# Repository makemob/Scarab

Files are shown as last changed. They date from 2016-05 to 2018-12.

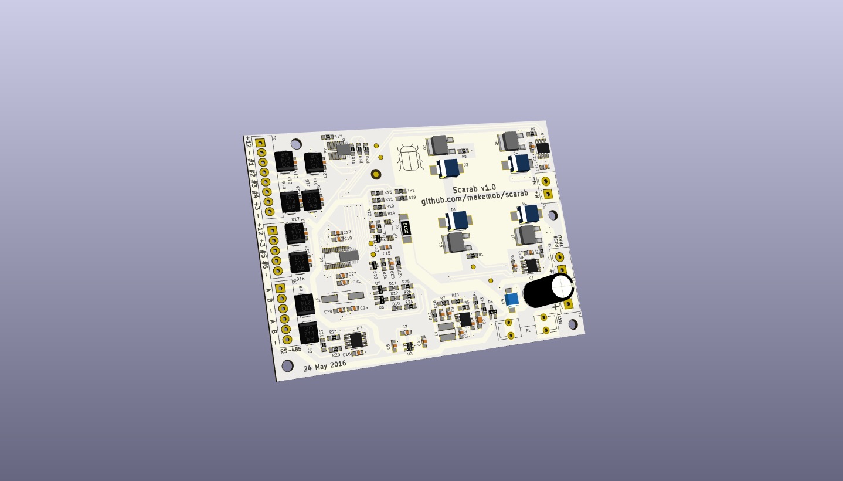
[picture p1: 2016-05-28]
v1.0/Docs/Scarab v1.0 3D Front 4.jpg

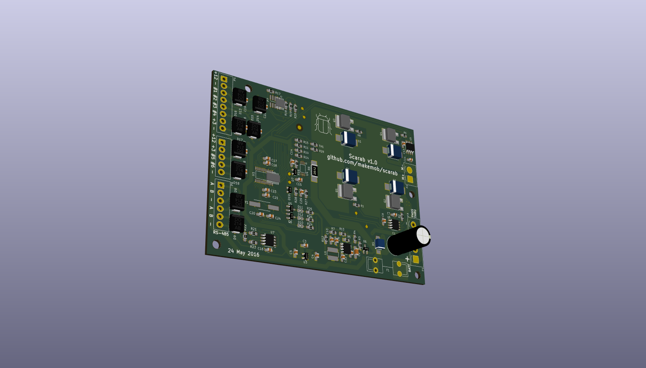
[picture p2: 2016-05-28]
v1.0/Docs/Scarab v1.0 3D Front 1.png

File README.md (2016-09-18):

# Scarab
H-Bridge motor/actuator controller with RS-485 comms

- Based around NXP LPC1114 Microcontroller
- 13-48VDC input (36V nominal)
- 8A average current output
- 12VDC max 200mA auxiliary output
- 3.3VDC auxiliary output ~40mA at 25 deg C, <10mA at 85 deg C
- Good to 85 deg C ambient (in theory)
- RS-485 comms, aux analog and digital I/O
- 3 x indicator LEDs
- NTC temperature sensor
- Battery voltage sensing

All specifications are indicative..

Designed to drive Linak LA-35 linear actuators for the MakeMob UKI - Utility Kinetic Insect project http://makemob.net/portfolio_page/uki-electric-insect-vehicle/

Suitable for all kinds of other clever tricks

Firmware available at http://github.com/makemob/huhu

Licensed under Creative Commons Attribution Share Alike 4.0, https://creativecommons.org/licenses/by-sa/4.0/legalcode.txt

BOM adjustments since v1.0:
- Replace R1, R2, R8, R9 with 100ohm
- Populate D7 (3V zener), C14 (10nF), D15 & D16 (5V TVS), C25 & C26 (100nF)
- RC snubber across motor output may be required to protect gate drivers from overvoltage (it is if you want to run LA-35 actuators at 36V..)

Next time:
- Locating C1 closer to the bridge may improve transients
- BAV99 footprints are wrong, need to jam them on sideways (D6, D7, D19)

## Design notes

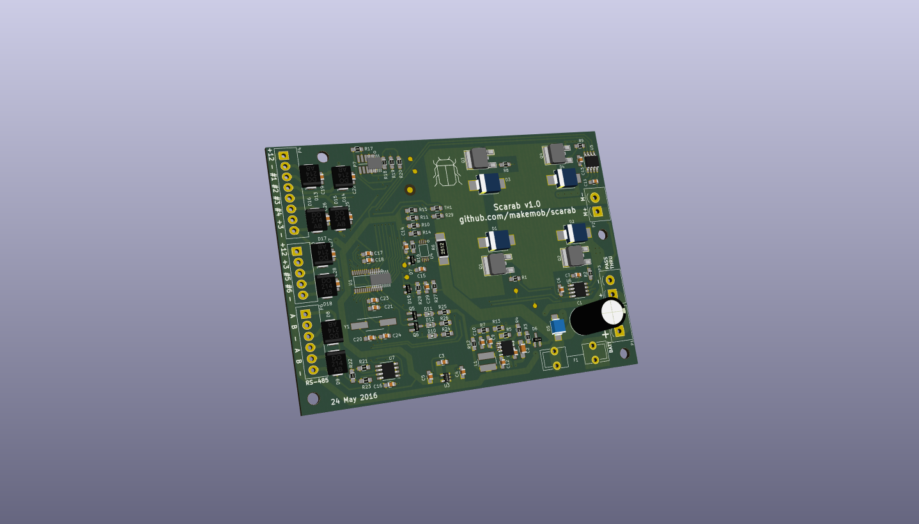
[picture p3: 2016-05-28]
v1.0/Docs/Scarab v1.0 3D Front 3.png

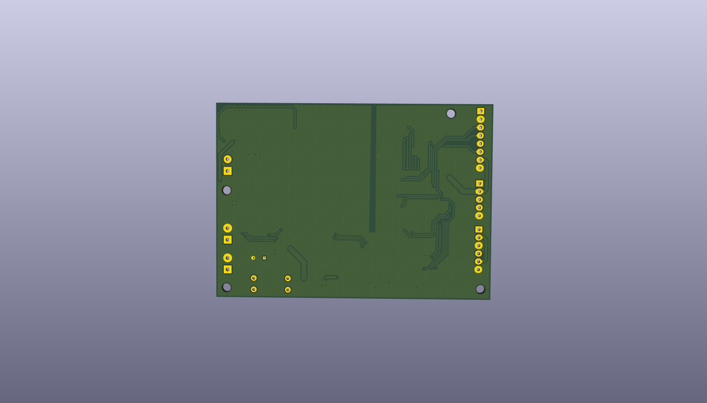
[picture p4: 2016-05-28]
v1.0/Docs/Scarab v1.0 3D Back 1.png

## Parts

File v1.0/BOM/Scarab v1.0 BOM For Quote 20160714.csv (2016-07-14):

Reference | Value | Footprint | Datasheet
P1 | BATT | BugBridgePCBLib:Connector_5.08mm_Pitch_2way
P2 | MOTOR | BugBridgePCBLib:Connector_5.08mm_Pitch_2way
P4 | AUX_A | BugBridgePCBLib:Connector_3.5mm_Pitch_8way
P6 | COMMS | BugBridgePCBLib:Connector_3.5mm_Pitch_6way
P3 | PASSTHRU | BugBridgePCBLib:Connector_5.08mm_Pitch_2way
P5 | AUX_B | BugBridgePCBLib:Connector_3.5mm_Pitch_5way
C8 | 10nF | Capacitors_SMD:C_0805_HandSoldering
C2 | 2.2uF | Capacitors_SMD:C_1206_HandSoldering
C9 | 68pF | Capacitors_SMD:C_0805_HandSoldering
R3 | NF | Resistors_SMD:R_0805_HandSoldering
R4 | NF | Resistors_SMD:R_0805_HandSoldering
R12 | 140k | Resistors_SMD:R_0805_HandSoldering
R13 | 10k | Resistors_SMD:R_0805_HandSoldering
L1 | 220uH 1.57R | BugBridgePCBLib:INDUCTOR_SDR0604
C12 | 10uF | Capacitors_SMD:C_0805_HandSoldering
U2 | TPS54061 | BugBridgePCBLib:VSON8
R7 | 158k | Resistors_SMD:R_0805_HandSoldering
C10 | 750pF | Capacitors_SMD:C_0805_HandSoldering
R5 | 97.6k | Resistors_SMD:R_0805_HandSoldering
F1 | 8A | BugBridgePCBLib:Fuseholder_5x20_Schurter
U3 | MIC5205-3.3YM5 | TO_SOT_Packages_SMD:SOT-23-5
C4 | 1uF | Capacitors_SMD:C_0805_HandSoldering
C3 | NF | Capacitors_SMD:C_0805_HandSoldering
C5 | 1uF | Capacitors_SMD:C_0805_HandSoldering
Q1 | IPD35N10S3L-26 | TO_SOT_Packages_SMD:TO-252-2Lead
Q2 | IPD35N10S3L-26 | TO_SOT_Packages_SMD:TO-252-2Lead
Q3 | IPD35N10S3L-26 | TO_SOT_Packages_SMD:TO-252-2Lead
Q4 | IPD35N10S3L-26 | TO_SOT_Packages_SMD:TO-252-2Lead
R6 | 0.01R 1W | Resistors_SMD:R_2512_HandSoldering
R8 | 0R | Resistors_SMD:R_0805_HandSoldering
R9 | 0R | Resistors_SMD:R_0805_HandSoldering
R1 | 0R | Resistors_SMD:R_0805_HandSoldering
R2 | 0R | Resistors_SMD:R_0805_HandSoldering
D1 | NF | Diodes_SMD:SMC_Handsoldering
D3 | NF | Diodes_SMD:SMC_Handsoldering
D4 | NF | Diodes_SMD:SMC_Handsoldering
D2 | NF | Diodes_SMD:SMC_Handsoldering
U4 | ST_CS70 | BugBridgePCBLib:TSSOP8
C15 | 100nF | Capacitors_SMD:C_0805_HandSoldering
R10 | NF | Resistors_SMD:R_0805_HandSoldering
R11 | 0R | Resistors_SMD:R_0805_HandSoldering
R14 | NF | Resistors_SMD:R_0805_HandSoldering
R15 | 0R | Resistors_SMD:R_0805_HandSoldering
R16 | 1k | Resistors_SMD:R_0805_HandSoldering
C14 | NF | Capacitors_SMD:C_0805_HandSoldering
D7 | NF | TO_SOT_Packages_SMD:SOT-23
U5 | MIC4605-1YM | BugBridgePCBLib:SOIC-8_Pitch1.27mm
U6 | MIC4605-1YM | BugBridgePCBLib:SOIC-8_Pitch1.27mm
C11 | 1uF 25V X7R | Capacitors_SMD:C_0805_HandSoldering
C6 | 1uF 25V X7R | Capacitors_SMD:C_0805_HandSoldering
C13 | 1uF 25V X7R | Capacitors_SMD:C_0805_HandSoldering
C7 | 1uF 25V X7R | Capacitors_SMD:C_0805_HandSoldering
D6 | BAV99 | TO_SOT_Packages_SMD:SOT-23_Handsoldering
C1 | 150uF | Capacitors_ThroughHole:C_Radial_D10_L20_P5
D5 | TVS | Diodes_SMD:SMB_Handsoldering
Y1 | 12MHz 20pF | BugBridgePCBLib:Crystal_FOX_HC
C20 | 39pF | Capacitors_SMD:C_0805_HandSoldering
C24 | 39pF | Capacitors_SMD:C_0805_HandSoldering
C21 | 100nF | Capacitors_SMD:C_0805_HandSoldering
C23 | 10nF | Capacitors_SMD:C_0805_HandSoldering
C17 | 100nF | Capacitors_SMD:C_0805_HandSoldering
C18 | 10nF | Capacitors_SMD:C_0805_HandSoldering
P7 | ISP | BugBridgePCBLib:CON_02X05_1.27
R18 | 47k | Resistors_SMD:R_0805_HandSoldering
R19 | 47k | Resistors_SMD:R_0805_HandSoldering
R20 | NF | Resistors_SMD:R_0805_HandSoldering
U7 | MAX3485 | BugBridgePCBLib:SOIC-8_Pitch1.27mm
C16 | 100nF | Capacitors_SMD:C_0805_HandSoldering
R21 | NF | Resistors_SMD:R_0805_HandSoldering
R22 | NF | Resistors_SMD:R_0805_HandSoldering
R23 | NF | Resistors_SMD:R_0805_HandSoldering
D8 | TVS 12V | BugBridgePCBLib:DO-214AC_Handsoldering
D9 | TVS 12V | BugBridgePCBLib:DO-214AC_Handsoldering
U1 | LPC1114FDH28/102 | BugBridgePCBLib:TSSOP-28
R17 | 0R | Resistors_SMD:R_0805_HandSoldering
TH1 | NTCS0805E3103JMT | Resistors_SMD:R_0805_HandSoldering
R29 | 10k | Resistors_SMD:R_0805_HandSoldering
R27 | 120k | Resistors_SMD:R_0805_HandSoldering
R28 | 10k | Resistors_SMD:R_0805_HandSoldering
C29 | 10nF | Capacitors_SMD:C_0805_HandSoldering
D19 | 3V | TO_SOT_Packages_SMD:SOT-23
D12 | GREEN | LEDs:LED_0805
D10 | RED | LEDs:LED_0805
D11 | BLUE | LEDs:LED_0805
R24 | 1k8 | Resistors_SMD:R_0805_HandSoldering
R25 | 1k8 | Resistors_SMD:R_0805_HandSoldering
R26 | 1k8 | Resistors_SMD:R_0805_HandSoldering
Q5 | MMUN2211LT1G | TO_SOT_Packages_SMD:SOT-23_Handsoldering
Q6 | MMUN2211LT1G | TO_SOT_Packages_SMD:SOT-23_Handsoldering
D13 | NF | BugBridgePCBLib:DO-214AC_Handsoldering
D14 | NF | BugBridgePCBLib:DO-214AC_Handsoldering
D15 | NF | BugBridgePCBLib:DO-214AC_Handsoldering
D16 | NF | BugBridgePCBLib:DO-214AC_Handsoldering
D17 | NF | BugBridgePCBLib:DO-214AC_Handsoldering
D18 | NF | BugBridgePCBLib:DO-214AC_Handsoldering
C19 | NF | Capacitors_SMD:C_0805_HandSoldering
C22 | NF | Capacitors_SMD:C_0805_HandSoldering
C25 | NF | Capacitors_SMD:C_0805_HandSoldering
C26 | NF | Capacitors_SMD:C_0805_HandSoldering
C27 | NF | Capacitors_SMD:C_0805_HandSoldering
C28 | NF | Capacitors_SMD:C_0805_HandSoldering

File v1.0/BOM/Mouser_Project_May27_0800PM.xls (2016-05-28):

Scarab v1.0
Mouser # | Mfr. # | Manufacturer | Desc. | RoHS | Lifecycle | Customer Part # | Order Qty. | Price (AUD) | Ext.: (AUD)
511-CS70P | CS70P | STMicroelectronics | Current Sense Amplifiers ANALOG | RoHS Compliant |  |  | 3 | $2.85 | $8.55
512-SMBJ64CA | SMBJ64CA | Fairchild Semiconductor | TVS Diodes - Transient Voltage Suppressors 600W TVS Diode Bidirectional | RoHS Compliant By Exemption |  |  | 3 | $0.56 | $1.68
530-5ST8-R | 5ST 8-R | Bel | Cartridge Fuses Fuse | RoHS Compliant |  |  | 5 | $0.336 | $1.68
559-FOXSDLF/120R-20 | FOXSDLF/120R-20/TR | Fox | Crystals 12MHz 20pF '-40C +85C | RoHS Compliant |  |  | 3 | $0.576 | $1.73
581-08051A680F | 08051A680FAT2A | AVX | Multilayer Ceramic Capacitors MLCC - SMD/SMT 0805 68pF 100volts C0G 1% | RoHS Compliant |  |  | 10 | $0.16 | $1.60
581-08055A390J | 08055A390JAT2A | AVX | Multilayer Ceramic Capacitors MLCC - SMD/SMT 0805 39pF 50volts C0G 5% | RoHS Compliant |  |  | 20 | $0.16 | $3.20
581-SMAJ12CA | SMAJ12CA | AVX | TVS Diodes - Transient Voltage Suppressors 12volts 400watts BiDirectional | RoHS Compliant |  |  | 6 | $0.512 | $3.07
594-2381-615-53103 | NTCS0805E3103JMT | Vishay | NTC Thermistors 10K OHM 5% | RoHS Compliant |  |  | 3 | $0.256 | $0.77
595-TPS54061DRBR | TPS54061DRBR | Texas Instruments | Voltage Regulators - Switching Regulators 4.7-60V,200mA Sync SD Converter | RoHS Compliant |  |  | 3 | $4.42 | $13.26
647-UPW1J151MPD | UPW1J151MPD | Nichicon | Aluminum Electrolytic Capacitors - Leaded 63volts 150uF 10x16 20% 5LS | RoHS Compliant |  |  | 3 | $0.592 | $1.78
649-202112100010C4LF | 20021121-00010C4LF | FCI / Amphenol | Headers & Wire Housings 1.27x1.27mm BTB, Hdr Unshrd, SMT, 10 Pos | RoHS Compliant |  |  | 3 | $1.15 | $3.45
649-220107-C051A01LF | 20020107-C051A01LF | FCI / Amphenol | Pluggable Terminal Blocks 5P 3.50MM HDR STRT PLUGGABLE TERM BLK | RoHS Compliant |  |  | 3 | $0.896 | $2.69
649-220107-C061A01LF | 20020107-C061A01LF | FCI / Amphenol | Pluggable Terminal Blocks 6P 3.50MM HDR STRT PLUGGABLE TERM BLK | RoHS Compliant |  |  | 3 | $1.07 | $3.21
649-220107-C081A01LF | 20020107-C081A01LF | FCI / Amphenol | Pluggable Terminal Blocks 8P 3.50MM HDR STRT PLUGGABLE TERM BLK | RoHS Compliant |  |  | 3 | $1.28 | $3.84
652-SDR0604-221KL | SDR0604-221KL | Bourns | Fixed Inductors 220uH 10% SMD 0604 | RoHS Compliant |  |  | 10 | $0.541 | $5.41
700-MAX3485CSA | MAX3485CSA+ | Maxim Integrated | RS-422/RS-485 Interface IC 3.3V 10Mbps Transceiver | RoHS Compliant |  |  | 3 | $4.64 | $13.92
71-CRCW0805-0-E3 | CRCW08050000Z0EA | Vishay | Thick Film Resistors - SMD 1/8watt ZEROohm Jumper | RoHS Compliant By Exemption |  |  | 100 | $0.038 | $3.80
71-CRCW0805-1.0K-E3 | CRCW08051K00FKEA | Vishay | Thick Film Resistors - SMD 1/8watt 1Kohms 1% 100ppm | RoHS Compliant By Exemption |  |  | 10 | $0.078 | $0.78
71-CRCW0805-1.8K-E3 | CRCW08051K80FKEA | Vishay | Thick Film Resistors - SMD 1/8watt 1.8Kohms 1% 100ppm | RoHS Compliant By Exemption |  |  | 10 | $0.078 | $0.78
71-CRCW0805-10K-E3 | CRCW080510K0FKEA | Vishay | Thick Film Resistors - SMD 1/8watt 10Kohms 1% 100ppm | RoHS Compliant By Exemption |  |  | 10 | $0.078 | $0.78
71-CRCW0805-140K-E3 | CRCW0805140KFKEA | Vishay | Thick Film Resistors - SMD 1/8watt 140Kohms 1% 100ppm | RoHS Compliant By Exemption |  |  | 10 | $0.078 | $0.78
71-CRCW0805-47K-E3 | CRCW080547K0FKEA | Vishay | Thick Film Resistors - SMD 1/8watt 47Kohms 1% 100ppm | RoHS Compliant By Exemption |  |  | 10 | $0.078 | $0.78
71-CRCW0805-97.6K-E3 | CRCW080597K6FKEA | Vishay | Thick Film Resistors - SMD 1/8watt 97.6Kohms 1% 100ppm | RoHS Compliant By Exemption |  |  | 10 | $0.078 | $0.78
71-CRCW0805120KFKEA | CRCW0805120KFKEA | Vishay | Thick Film Resistors - SMD 1/8watt 120Kohms 1% 100ppm | RoHS Compliant By Exemption |  |  | 10 | $0.078 | $0.78
71-CRCW0805158KFKEA | CRCW0805158KFKEA | Vishay | Thick Film Resistors - SMD 1/8watt 158Kohms 1% 100ppm | RoHS Compliant By Exemption |  |  | 10 | $0.078 | $0.78
710-691311500102 | 691311500102 | Wurth Electronics | Pluggable Terminal Blocks WR-TBL PCB Model 311 2Pin 5.08mm Cls Vtcl | RoHS Compliant |  |  | 10 | $0.44 | $4.40
710-885012207072 | 885012207072 | Wurth Electronics | Multilayer Ceramic Capacitors MLCC - SMD/SMT WCAP-CSGP 100000pF 0805 10% 25V MLCC | RoHS Compliant |  |  | 50 | $0.064 | $3.20
710-885012207092 | 885012207092 | Wurth Electronics | Multilayer Ceramic Capacitors MLCC - SMD/SMT WCAP-CSGP 10000pF 0805 10% 50V MLCC | RoHS Compliant |  |  | 50 | $0.08 | $4.00
726-IPD35N10S3L26 | IPD35N10S3L-26 | Infineon | MOSFET N-Ch 100V 35A DPAK-2 OptiMOS-T | RoHS Compliant |  |  | 16 | $1.19 | $19.04
756-LRMAM2512R01FT4 | LRMAM2512-R01FT4 | TT Electronics | Current Sense Resistors - SMD 2512 10mOhms 1% Low Thermal | RoHS Compliant |  |  | 3 | $0.608 | $1.82
771-LPC1114FDH28/102 | LPC1114FDH28/102:5 | NXP | ARM Microcontrollers - MCU CortexM0 32bit 32KB | RoHS Compliant |  |  | 3 | $3.94 | $11.82
81-GRM2165C1H751JA | GRM2165C1H751JA01D | Murata | Multilayer Ceramic Capacitors MLCC - SMD/SMT 0805 750pF 50volts C0G 5% | RoHS Compliant |  |  | 10 | $0.122 | $1.22
81-GRM21BR61E106MA3L | GRM21BR61E106MA73L | Murata | Multilayer Ceramic Capacitors MLCC - SMD/SMT 0805 10uF 25volts X5R 20% | RoHS Compliant | New Product |  | 10 | $0.138 | $1.38
81-GRM31CR72A225KA3L | GRM31CR72A225KA73L | Murata | Multilayer Ceramic Capacitors MLCC - SMD/SMT 1206 2.2uF 100volts X7R 10% | RoHS Compliant | New Product |  | 10 | $0.512 | $5.12
810-C2012X7R1E105K | C2012X7R1E105K125AB | TDK | Multilayer Ceramic Capacitors MLCC - SMD/SMT 0805 1uF 25volts X7R 10% | RoHS Compliant |  |  | 100 | $0.048 | $4.80
859-LTST-C170TBKT | LTST-C170TBKT | Lite-On | Standard LEDs - SMD Blue Clear 466nm | RoHS Compliant |  |  | 10 | $0.443 | $4.43
859-LTST-C171GKT | LTST-C171GKT | Lite-On | Standard LEDs - SMD Green Clear 569nm | RoHS Compliant |  |  | 10 | $0.381 | $3.81
859-LTST-C171KRKT | LTST-C171KRKT | Lite-On | Standard LEDs - SMD Red Clear 55MCD | RoHS Compliant |  |  | 10 | $0.397 | $3.97
863-BAV99LT1G | BAV99LT1G | ON Semiconductor | Diodes - General Purpose, Power, Switching 70V 215mA Dual | RoHS Compliant |  |  | 10 | $0.17 | $1.70
863-BZX84C3V0LT1G | BZX84C3V0LT1G | ON Semiconductor | Zener Diodes 3.0V 225mW | RoHS Compliant |  |  | 10 | $0.20 | $2.00
863-MMUN2211LT1G | MMUN2211LT1G | ON Semiconductor | Bipolar Transistors - Pre-Biased 100mA 50V BRT NPN | RoHS Compliant |  |  | 10 | $0.179 | $1.79
998-MIC4605-1YM | MIC4605-1YM | Microchip | Gate Drivers 85V Half Bridge MOSFET Driver | RoHS Compliant | New At Mouser |  | 10 | $1.25 | $12.50
998-MIC5205-3.3YM5TR | MIC5205-3.3YM5-TR | Microchip | LDO Voltage Regulators | RoHS Compliant |  |  | 10 | $0.64 | $6.40
693-0751.0062 | 751.0062 | Schurter | Fuse Clips FUSE-CLIP OG BRASS | RoHS Compliant |  |  | 10 | $0.176 | $1.76
538-39500-0005 | 39500-0005 | Molex | Pluggable Terminal Blocks EURO 3.5MM HOR PLUG 5 CIRCUITS | RoHS Compliant |  |  | 3 | $2.29 | $6.87
538-39500-0006 | 39500-0006 | Molex | Pluggable Terminal Blocks 6CKT HORIZ PLUG | RoHS Compliant |  |  | 3 | $2.72 | $8.16
538-39503-2008 | 39503-2008 | Molex | Pluggable Terminal Blocks 3.50MM EURO PLUG VER UG VERT RWE BLK 8CKT | RoHS Compliant |  |  | 3 | $3.79 | $11.37
649-202007H021B01LF | 20020007-H021B01LF | FCI / Amphenol | Pluggable Terminal Blocks 2P PLUGGABLE PLUG FLANGE, 5.08mm PITCH | RoHS Compliant |  |  | 10 | $1.13 | $11.30

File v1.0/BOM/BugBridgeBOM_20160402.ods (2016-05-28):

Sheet: Sheet1
BugBridge BOM 20160402
Reference | Value | Mouser | Price | Mating Part | Price
C1 | 150uF | 647-UPW1J151MPD | 0.592
C10 | 750pF | 81-GRM2165C1H751JA | 0.122
C11 | 1uF 25V X7R | 810-C2012X7R1E105K | 0.082
C12 | 10uF | 81-GRM21BR61E106MA3L | 0.138
C13 | 1uF 25V X7R | 810-C2012X7R1E105K | 0.082
C14 | NF | -
C15 | 100nF | 710-885012207072 | 0.08
C16 | 100nF | 710-885012207072 | 0.08
C17 | 100nF | 710-885012207072 | 0.08
C18 | 10nF | 710-885012207092 | 0.112
C19 | NF | -
C2 | 2.2uF | 81-GRM31CR72A225KA3L | 0.534
C20 | 39pF | 581-08055A390J | 0.16
C21 | 100nF | 710-885012207072 | 0.08
C22 | NF | -
C23 | 10nF | 710-885012207092 | 0.112
C24 | 39pF | 581-08055A390J | 0.16
C25 | NF | -
C26 | NF | -
C27 | NF | -
C28 | NF | -
C29 | 10nF | 710-885012207092 | 0.112
C3 | NF | -
C4 | 1uF | 810-C2012X7R1E105K | 0.082
C5 | 1uF | 810-C2012X7R1E105K | 0.082
C6 | 1uF 25V X7R | 810-C2012X7R1E105K | 0.082
C7 | 1uF 25V X7R | 810-C2012X7R1E105K | 0.082
C8 | 10nF | 710-885012207092 | 0.112
C9 | 68pF | 581-08051A680F | 0.16
D1 | NF | -
D10 | RED | 859-LTST-C171KRKT | 0.397
D11 | BLUE | 859-LTST-C170TBKT | 0.443
D12 | GREEN | 859-LTST-C171GKT | 0.381
D13 | NF | -
D14 | NF | -
D15 | NF | -
D16 | NF | -
D17 | NF | -
D18 | NF | -
D19 | 3V | 863-BZX84C3V0LT1G | 0.2
D2 | NF | -
D3 | NF | -
D4 | NF | -
D5 | TVS | 512-SMBJ64CA | 0.429
D6 | BAV99 | 863-BAV99LT1G | 0.17
D7 | NF | -
D8 | TVS 12V | 581-SMAJ12CA | 0.512
D9 | TVS 12V | 581-SMAJ12CA | 0.512
F1 | 8A | 530-5ST8-R | 0.323 | 2 x 693-0751.0062 | 0.352
L1 | 220uH 1.57R | 652-SDR0604-221KL | 0.541
P1 | BATT | 710-691311500102 | 0.44 | 649-202007H021B01LF | 1.13
P2 | MOTOR | 710-691311500102 | 0.44 | 649-202007H021B01LF | 1.13
P3 | PASSTHRU | 710-691311500102 | 0.44 | 649-202007H021B01LF | 1.13
P4 | AUX_A | 649-220107-C081A01LF | 1.14 | 538-39503-2008 | 3.44
P5 | AUX_B | 649-220107-C051A01LF | 0.842 | 538-39500-0005 | 2.29
P6 | COMMS | 649-220107-C061A01LF | 1.01 | 538-39500-0006 | 2.72
P7 | ISP | 649-202112100010C4LF | 1.02
Q1 | IPD35N10S3L-26 | 726-IPD35N10S3L26 | 1.19
Q2 | IPD35N10S3L-26 | 726-IPD35N10S3L26 | 1.19
Q3 | IPD35N10S3L-26 | 726-IPD35N10S3L26 | 1.19
Q4 | IPD35N10S3L-26 | 726-IPD35N10S3L26 | 1.19
Q5 | MMUN2211LT1G | 863-MMUN2211LT1G | 0.179
Q6 | MMUN2211LT1G | 863-MMUN2211LT1G | 0.179
R1 | 0R | 71-CRCW0805-0-E3 | 0.067
R10 | NF | -
R11 | 0R | 71-CRCW0805-0-E3 | 0.067
R12 | 140k | 71-CRCW0805-140K-E3 | 0.078
R13 | 10k | 71-CRCW0805-10K-E3 | 0.078
R14 | NF | -
R15 | 0R | 71-CRCW0805-0-E3 | 0.067
R16 | 1k | 71-CRCW0805-1.0K-E3 | 0.078
R17 | 0R | 71-CRCW0805-0-E3 | 0.067
R18 | 47k | 71-CRCW0805-47K-E3 | 0.078
R19 | 47k | 71-CRCW0805-47K-E3 | 0.078
R2 | 0R | 71-CRCW0805-0-E3 | 0.067
R20 | NF | -
R21 | NF | -
R22 | NF | -
R23 | NF | -
R24 | 1k8 | 71-CRCW0805-1.8K-E3 | 0.078
R25 | 1k8 | 71-CRCW0805-1.8K-E3 | 0.078
R26 | 1k8 | 71-CRCW0805-1.8K-E3 | 0.078
R27 | 120k | 71-CRCW0805120KFKEA | 0.078
R28 | 10k | 71-CRCW0805-10K-E3 | 0.078
R29 | 10k | 71-CRCW0805-10K-E3 | 0.078
R3 | NF | -
R4 | NF | -
R5 | 97.6k | 71-CRCW0805-97.6K-E3 | 0.078
R6 | 0.01R 1W | 756-LRMAM2512R01FT4 | 0.608
R7 | 158k | 71-CRCW0805158KFKEA | 0.078
R8 | 0R | 71-CRCW0805-0-E3 | 0.067
R9 | 0R | 71-CRCW0805-0-E3 | 0.067
TH1 | NTCS0805E3103JMT | 594-2381-615-53103 | 0.256
U1 | LPC1114FDH28/102 | 771-LPC1114FDH28/102 | 2.37
U2 | TPS54061 | 595-TPS54061DRBR | 3.97
U3 | MIC5205-3.3YM5 | 998-MIC5205-3.3YM5TR | 0.64
U4 | ST_CS70 | 511-CS70P | 2.42
U5 | MIC4605-1YM | 998-MIC4605-1YM | 1.25
U6 | MIC4605-1YM | 998-MIC4605-1YM | 1.25
U7 | MAX3485 | 700-MAX3485CSA | 4.4
Y1 | 12MHz 20pF | 559-FOXSDLF/120R-20 | 0.496
PCB |  |  | 2.5
 |  | Total with minimal connectors: | 42.037
 |  | Total with all connectors: | 51.319
 |  | Extra connectors: | 9.282

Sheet: Sheet2
Mouser order template
Part | Qty | Unit Price | Line Price
511-CS70P | 1 | 2.42 | 2.42
512-SMBJ64CA | 1 | 0.429 | 0.429
530-5ST8-R | 1 | 0.323 | 0.323
559-FOXSDLF/120R-20 | 1 | 0.496 | 0.496
581-08051A680F | 1 | 0.16 | 0.16 | bom <- read.csv("/Users/chrismock/Desktop/r/bugbridgebom.csv")
581-08055A390J | 2 | 0.16 | 0.32 | mating <- bom[ , c("Mating.Part", "Price.1")]
581-SMAJ12CA | 2 | 0.512 | 1.024 | bom <- bom[ , c("Mouser", "Price")]
594-2381-615-53103 | 1 | 0.256 | 0.256 | colnames(mating) <- c("Mouser", "Price")
595-TPS54061DRBR | 1 | 3.97 | 3.97 | bom <- rbind(bom, mating)
647-UPW1J151MPD | 1 | 0.592 | 0.592 | bom <- bom[apply(bom, 1, function(x) {!anyNA(x)}), ]
649-202112100010C4LF | 1 | 1.02 | 1.02
649-220107-C051A01LF | 1 | 0.842 | 0.842 | qty <- dplyr::summarise(dplyr::group_by(bom, Mouser), Qty = n())
649-220107-C061A01LF | 1 | 1.01 | 1.01
649-220107-C081A01LF | 1 | 1.14 | 1.14 | bomToOrder <- unique(dplyr::left_join(qty, bom, by = "Mouser"))
652-SDR0604-221KL | 1 | 0.541 | 0.541 | bomToOrder$LinePrice <- bomToOrder$Price * bomToOrder$Qty
700-MAX3485CSA | 1 | 4.4 | 4.4
71-CRCW0805-0-E3 | 7 | 0.067 | 0.469 | write.csv(bomToOrder, file = "/Users/chrismock/Desktop/r/bugbridgebomtoorder.csv")
71-CRCW0805-1.0K-E3 | 1 | 0.078 | 0.078
71-CRCW0805-1.8K-E3 | 3 | 0.078 | 0.234
71-CRCW0805-10K-E3 | 3 | 0.078 | 0.234 | (and edit 2 x fuse clips)
71-CRCW0805-140K-E3 | 1 | 0.078 | 0.078
71-CRCW0805-47K-E3 | 2 | 0.078 | 0.156
71-CRCW0805-97.6K-E3 | 1 | 0.078 | 0.078
71-CRCW0805120KFKEA | 1 | 0.078 | 0.078
71-CRCW0805158KFKEA | 1 | 0.078 | 0.078
710-691311500102 | 3 | 0.44 | 1.32
710-885012207072 | 4 | 0.08 | 0.32
710-885012207092 | 4 | 0.112 | 0.448
726-IPD35N10S3L26 | 4 | 1.19 | 4.76
756-LRMAM2512R01FT4 | 1 | 0.608 | 0.608
771-LPC1114FDH28/102 | 1 | 2.37 | 2.37
81-GRM2165C1H751JA | 1 | 0.122 | 0.122
81-GRM21BR61E106MA3L | 1 | 0.138 | 0.138
81-GRM31CR72A225KA3L | 1 | 0.534 | 0.534
810-C2012X7R1E105K | 6 | 0.082 | 0.492
859-LTST-C170TBKT | 1 | 0.443 | 0.443
859-LTST-C171GKT | 1 | 0.381 | 0.381
859-LTST-C171KRKT | 1 | 0.397 | 0.397
863-BAV99LT1G | 1 | 0.17 | 0.17
863-BZX84C3V0LT1G | 1 | 0.2 | 0.2
863-MMUN2211LT1G | 2 | 0.179 | 0.358
998-MIC4605-1YM | 2 | 1.25 | 2.5
998-MIC5205-3.3YM5TR | 1 | 0.64 | 0.64
693-0751.0062 | 2 | 0.352 | 0.352
538-39500-0005 | 1 | 2.29 | 2.29
538-39500-0006 | 1 | 2.72 | 2.72
538-39503-2008 | 1 | 3.44 | 3.44
649-202007H021B01LF | 3 | 1.13 | 3.39

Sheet: Sheet1_2
BugBridge BOM 20160402
Reference | Value | Mouser | Price | Mating Part | Price | Alternate | Price
C14 | NF | -
C19 | NF | -
C22 | NF | -
C25 | NF | -
C26 | NF | -
C27 | NF | -
C28 | NF | -
C3 | NF | -
D1 | NF | -
D13 | NF | -
D14 | NF | -
D15 | NF | -
D16 | NF | -
D17 | NF | -
D18 | NF | -
D2 | NF | -
D3 | NF | -
D4 | NF | -
D7 | NF | -
R10 | NF | -
R14 | NF | -
R20 | NF | -
R21 | NF | -
R22 | NF | -
R23 | NF | -
R3 | NF | -
R4 | NF | -
U4 | ST_CS70 | 511-CS70P | 2.42
D5 | TVS | 512-SMBJ64CA | 0.429
F1 | 8A | 530-5ST8-R | 0.323
Y1 | 12MHz 20pF | 559-FOXSDLF/120R-20 | 0.496
C9 | 68pF | 581-08051A680F | 0.16
C20 | 39pF | 581-08055A390J | 0.16
C24 | 39pF | 581-08055A390J | 0.16
D8 | TVS 12V | 581-SMAJ12CA | 0.512
D9 | TVS 12V | 581-SMAJ12CA | 0.512
TH1 | NTCS0805E3103JMT | 594-2381-615-53103 | 0.256
U2 | TPS54061 | 595-TPS54061DRBR | 3.97
C1 | 150uF | 647-UPW1J151MPD | 0.592
P7 | ISP | 649-202112100010C4LF | 1.02
P5 | AUX_B | 649-220107-C051A01LF | 0.842
P6 | COMMS | 649-220107-C061A01LF | 1.01
P4 | AUX_A | 649-220107-C081A01LF | 1.14
L1 | 220uH 1.57R | 652-SDR0604-221KL | 0.541
U7 | MAX3485 | 700-MAX3485CSA | 4.4
R1 | 0R | 71-CRCW0805-0-E3 | 0.067
R11 | 0R | 71-CRCW0805-0-E3 | 0.067
R15 | 0R | 71-CRCW0805-0-E3 | 0.067
R17 | 0R | 71-CRCW0805-0-E3 | 0.067 | 2 x 693-0751.0062 | 0.352
R2 | 0R | 71-CRCW0805-0-E3 | 0.067
R8 | 0R | 71-CRCW0805-0-E3 | 0.067 | 649-202007H021B01LF | 1.13
R9 | 0R | 71-CRCW0805-0-E3 | 0.067 | 649-202007H021B01LF | 1.13
R16 | 1k | 71-CRCW0805-1.0K-E3 | 0.078 | 649-202007H021B01LF | 1.13
R24 | 1k8 | 71-CRCW0805-1.8K-E3 | 0.078 | 538-39503-2008 | 3.44
R25 | 1k8 | 71-CRCW0805-1.8K-E3 | 0.078 | 538-39500-0005 | 2.29
R26 | 1k8 | 71-CRCW0805-1.8K-E3 | 0.078 | 538-39500-0006 | 2.72
R13 | 10k | 71-CRCW0805-10K-E3 | 0.078
R28 | 10k | 71-CRCW0805-10K-E3 | 0.078
R29 | 10k | 71-CRCW0805-10K-E3 | 0.078
R12 | 140k | 71-CRCW0805-140K-E3 | 0.078
R18 | 47k | 71-CRCW0805-47K-E3 | 0.078
R19 | 47k | 71-CRCW0805-47K-E3 | 0.078
R5 | 97.6k | 71-CRCW0805-97.6K-E3 | 0.078
R27 | 120k | 71-CRCW0805120KFKEA | 0.078
R7 | 158k | 71-CRCW0805158KFKEA | 0.078
P1 | BATT | 710-691311500102 | 0.44
P2 | MOTOR | 710-691311500102 | 0.44
P3 | PASSTHRU | 710-691311500102 | 0.44
C15 | 100nF | 710-885012207072 | 0.08
C16 | 100nF | 710-885012207072 | 0.08
C17 | 100nF | 710-885012207072 | 0.08
C21 | 100nF | 710-885012207072 | 0.08
C18 | 10nF | 710-885012207092 | 0.112 |  |  | 581-12065C103KAT4A | 0.16
C23 | 10nF | 710-885012207092 | 0.112 |  |  | 581-12065C103KAT4A | 0.16
C29 | 10nF | 710-885012207092 | 0.112 |  |  | 581-12065C103KAT4A | 0.16
C8 | 10nF | 710-885012207092 | 0.112 |  |  | 581-12065C103KAT4A | 0.16
Q1 | IPD35N10S3L-26 | 726-IPD35N10S3L26 | 1.19
Q2 | IPD35N10S3L-26 | 726-IPD35N10S3L26 | 1.19
Q3 | IPD35N10S3L-26 | 726-IPD35N10S3L26 | 1.19
Q4 | IPD35N10S3L-26 | 726-IPD35N10S3L26 | 1.19
R6 | 0.01R 1W | 756-LRMAM2512R01FT4 | 0.608
U1 | LPC1114FDH28/102 | 771-LPC1114FDH28/102 | 2.37
C10 | 750pF | 81-GRM2165C1H751JA | 0.122
C12 | 10uF | 81-GRM21BR61E106MA3L | 0.138
C2 | 2.2uF | 81-GRM31CR72A225KA3L | 0.534
C11 | 1uF 25V X7R | 810-C2012X7R1E105K | 0.082
C13 | 1uF 25V X7R | 810-C2012X7R1E105K | 0.082
C4 | 1uF | 810-C2012X7R1E105K | 0.082
C5 | 1uF | 810-C2012X7R1E105K | 0.082
C6 | 1uF 25V X7R | 810-C2012X7R1E105K | 0.082
C7 | 1uF 25V X7R | 810-C2012X7R1E105K | 0.082
D11 | BLUE | 859-LTST-C170TBKT | 0.443
D12 | GREEN | 859-LTST-C171GKT | 0.381
D10 | RED | 859-LTST-C171KRKT | 0.397
D6 | BAV99 | 863-BAV99LT1G | 0.17
D19 | 3V | 863-BZX84C3V0LT1G | 0.2
Q5 | MMUN2211LT1G | 863-MMUN2211LT1G | 0.179
Q6 | MMUN2211LT1G | 863-MMUN2211LT1G | 0.179
U5 | MIC4605-1YM | 998-MIC4605-1YM | 1.25
U6 | MIC4605-1YM | 998-MIC4605-1YM | 1.25
U3 | MIC5205-3.3YM5 | 998-MIC5205-3.3YM5TR | 0.64
PCB |  |  | 2.5
 |  | Total with minimal connectors: | 44.225
 |  | Total with all connectors: | 51.319
 |  | Extra connectors: | 7.094

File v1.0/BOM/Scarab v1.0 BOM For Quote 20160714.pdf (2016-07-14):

Sheet1

## Scarab v1.0 BOM 20160714

Preferred parts listed with Mouser order number Substitutions accepted with prior approval
Do not quote no-fit parts (marked NF)
Reference Value | Footprint | Mouser No.
C1 | 150uF | C_Radial_D10_L20_P | 647-UPW1J151MPD
C10 | 750pF | 0805 | 81-GRM2165C1H751JA
C11 | 1uF 25V X7R | 0805 | 810-C2012X7R1E105K
C12 | 10uF | 0805 | 81-GRM21BR61E106MA3L
C13 | 1uF 25V X7R | 0805 | 810-C2012X7R1E105K
C14 | NF | 0805 | -
C15 | 100nF | 0805 | 710-885012207072
C16 | 100nF | 0805 | 710-885012207072
C17 | 100nF | 0805 | 710-885012207072
C18 | 10nF | 0805 | 710-885012207092
C19 | NF | 0805 | -
C2 | 2.2uF | 1206 | 81-GRM31CR72A225KA3L
C20 | 39pF | 0805 | 581-08055A390J
C21 | 100nF | 0805 | 710-885012207072
C22 | NF | 0805 | -
C23 | 10nF | 0805 | 710-885012207092
C24 | 39pF | 0805 | 581-08055A390J
C25 | NF | 0805 | -
C26 | NF | 0805 | -
C27 | NF | 0805 | -
C28 | NF | 0805 | -
C29 | 10nF | 0805 | 710-885012207092
C3 | NF | 0805 | -
C4 | 1uF | 0805 | 810-C2012X7R1E105K
C5 | 1uF | 0805 | 810-C2012X7R1E105K
C6 | 1uF 25V X7R | 0805 | 810-C2012X7R1E105K
C7 | 1uF 25V X7R | 0805 | 810-C2012X7R1E105K
C8 | 10nF | 0805 | 710-885012207092
C9 | 68pF | 0805 | 581-08051A680F
D1 | NF | SMC | -
D10 | RED | 0805 | 859-LTST-C171KRKT
D11 | BLUE | 0805 | 859-LTST-C170TBKT
D12 | GREEN | 0805 | 859-LTST-C171GKT
D13 | NF | DO-214AC | -
D14 | NF | DO-214AC | -
D15 | NF | DO-214AC | -
D16 | NF | DO-214AC | -
D17 | NF | DO-214AC | -
D18 | NF | DO-214AC | -
D19 | 3V | SOT-23 | 863-BZX84C3V0LT1G
D2 | NF | SMC | -
D3 | NF | SMC | -
D4 | NF | SMC | -
D5 | TVS | SMB | 512-SMBJ64CA
D6 | BAV99 | SOT-23 | 863-BAV99LT1G
D7 | NF | SOT-23 | -
D8 | TVS 12V | DO-214AC | 581-SMAJ12CA

D9 | TVS 12V | DO-214AC | 581-SMAJ12CA
F1 | 8A | | 2 x 693-0751.0062
L1 | 220uH 1.57R | INDUCTOR_SDR0604 | 652-SDR0604-221KL
P1 | BATT | 5.08mm_2way | 710-691311500102
P2 | MOTOR | 5.08mm_2way | 710-691311500102
P3 | NF | 5.08mm_2way | -
P4 | AUX_A | 3.5mm_8way | 649-220107-C081A01LF
P5 | AUX_B | 3.5mm_5way | 649-220107-C051A01LF
P6 | COMMS | 3.5mm_6way | 649-220107-C061A01LF
P7 | ISP | CON_02X05_1.27mm | 649-202112100010C4LF
Q1 | IPD35N10S3L-26 | TO-252 | 726-IPD35N10S3L26
Q2 | IPD35N10S3L-26 | TO-252 | 726-IPD35N10S3L26
Q3 | IPD35N10S3L-26 | TO-252 | 726-IPD35N10S3L26
Q4 | IPD35N10S3L-26 | TO-252 | 726-IPD35N10S3L26
Q5 | MMUN2211LT1G | SOT-23 | 863-MMUN2211LT1G
Q6 | MMUN2211LT1G | SOT-23 | 863-MMUN2211LT1G
R1 | 0R | 0805 | 71-CRCW0805-0-E3
R10 | NF | 0805 | -
R11 | 0R | 0805 | 71-CRCW0805-0-E3
R12 | 140k | 0805 | 71-CRCW0805-140K-E3
R13 | 10k | 0805 | 71-CRCW0805-10K-E3
R14 | NF | 0805 | -
R15 | 0R | 0805 | 71-CRCW0805-0-E3
R16 | 1k | 0805 | 71-CRCW0805-1.0K-E3
R17 | 0R | 0805 | 71-CRCW0805-0-E3
R18 | 47k | 0805 | 71-CRCW0805-47K-E3
R19 | 47k | 0805 | 71-CRCW0805-47K-E3
R2 | 0R | 0805 | 71-CRCW0805-0-E3
R20 | NF | 0805 | -
R21 | NF | 0805 | -
R22 | NF | 0805 | -
R23 | NF | 0805 | -
R24 | 1k8 | 0805 | 71-CRCW0805-1.8K-E3
R25 | 1k8 | 0805 | 71-CRCW0805-1.8K-E3
R26 | 1k8 | 0805 | 71-CRCW0805-1.8K-E3
R27 | 120k | 0805 | 71-CRCW0805120KFKEA
R28 | 10k | 0805 | 71-CRCW0805-10K-E3
R29 | 10k | 0805 | 71-CRCW0805-10K-E3
R3 | NF | 0805 | -
R4 | NF | 0805 | -
R5 | 97.6k | 0805 | 71-CRCW0805-97.6K-E3
R6 | 0.01R 1W | 2512 | 756-LRMAM2512R01FT4
R7 | 158k | 0805 | 71-CRCW0805158KFKEA
R8 | 0R | 0805 | 71-CRCW0805-0-E3
R9 | 0R | 0805 | 71-CRCW0805-0-E3
TH1 | NTCS0805E3103JMT 0805 | 594-2381-615-53103
U1 | LPC1114FDH28/102 | TSSOP-28 | 771-LPC1114FDH28/102
U2 | TPS54061 | VSON8 | 595-TPS54061DRBR
U3 | MIC5205-3.3YM5 | SOT-23-5 | 998-MIC5205-3.3YM5TR
U4 | ST_CS70 | TSSOP-8 | 511-CS70P
U5 | MIC4605-1YM | SOIC-8 | 998-MIC4605-1YM
U6 | MIC4605-1YM | SOIC-8 | 998-MIC4605-1YM
U7 | MAX3485 | SOIC-8 | 700-MAX3485CSA
Y1 | 12MHz 20pF | Crystal_FOX_HC | 559-FOXSDLF/120R-20

Fuseholder_5x20_Schurter

Manufacturer | Mating Part
| UPW1J151MPD
| GRM2165C1H751JA01D
TDK | C2012X7R1E105K125AB
| GRM21BR61E106MA73L
TDK | C2012X7R1E105K125AB
| 885012207072
| 885012207072
| 885012207072
| 885012207092
| GRM31CR72A225KA73L
AVX | 08055A390JAT2A
| 885012207072
| 885012207092
AVX | 08055A390JAT2A

885012207092

TDK | C2012X7R1E105K125AB
TDK | C2012X7R1E105K125AB
TDK | C2012X7R1E105K125AB
TDK | C2012X7R1E105K125AB
| 885012207092
AVX | 08051A680FAT2A
Lite-On | LTST-C171KRKT
Lite-On | LTST-C170TBKT
Lite-On | LTST-C171GKT
ON Semiconductor | BZX84C3V0LT1G

Fairchild Semiconductor SMBJ64CA
ON Semiconductor | BAV99LT1G
AVX | SMAJ12CA

Manf. Part No.
Nichicon
Murata

Murata

Wurth Electronics
Wurth Electronics
Wurth Electronics
Wurth Electronics

Murata

Wurth Electronics

Wurth Electronics

Wurth Electronics

Wurth Electronics

AVX | SMAJ12CA
751.0062 | 530-5ST8-R
Bourns | SDR0604-221KL
691311500102 | 649-202007H021B01LF
691311500102 | 649-202007H021B01LF
20020107-C081A01LF | 538-39503-2008
20020107-C051A01LF | 538-39500-0005
20020107-C061A01LF | 538-39500-0006
20021121-00010C4LF
Infineon | IPD35N10S3L-26
Infineon | IPD35N10S3L-26
Infineon | IPD35N10S3L-26
Infineon | IPD35N10S3L-26
ON Semiconductor | MMUN2211LT1G
ON Semiconductor | MMUN2211LT1G
CRCW08050000Z0EA

CRCW08050000Z0EA
CRCW0805140KFKEA
CRCW080510K0FKEA

CRCW08050000Z0EA
CRCW08051K00FKEA
CRCW08050000Z0EA
CRCW080547K0FKEA
CRCW080547K0FKEA
CRCW08050000Z0EA

CRCW08051K80FKEA
CRCW08051K80FKEA
CRCW08051K80FKEA
CRCW0805120KFKEA
CRCW080510K0FKEA
CRCW080510K0FKEA

CRCW080597K6FKEA
TT Electronics | LRMAM2512-R01FT4
| CRCW0805158KFKEA
| CRCW08050000Z0EA
| CRCW08050000Z0EA
| NTCS0805E3103JMT
NXP | LPC1114FDH28/102:5
Texas Instruments | TPS54061DRBR
Microchip | MIC5205-3.3YM5-TR
STMicroelectronics | CS70P
Microchip | MIC4605-1YM
Microchip | MIC4605-1YM
Maxim Integrated | MAX3485CSA+
Fox | FOXSDLF/120R-20/TR

Schurter

Wurth Electronics
Wurth Electronics

FCI / Amphenol
FCI / Amphenol
FCI / Amphenol
FCI / Amphenol

Vishay

Vishay
Vishay
Vishay

Vishay
Vishay
Vishay
Vishay
Vishay
Vishay

Vishay
Vishay
Vishay
Vishay
Vishay
Vishay

Vishay

Vishay
Vishay
Vishay
Vishay

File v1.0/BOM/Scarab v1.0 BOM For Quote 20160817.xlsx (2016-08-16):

Scarab v1.0 BOM 20160806
 |  |  |  |  | Build qty | 30
 | Preferred parts listed with Mouser order number
 | Substitutions accepted with prior approval
 | Do not quote no-fit parts (marked NF)
Reference | Value | Footprint | Mouser No. | Manufacturer | Manf. Part No. | Total Reqd | On Hand | Qty To Purchase
C1 | 150uF | C_Radial_D10_L20_P | 647-UPW1J151MPD | Nichicon | UPW1J151MPD | 30 |  | 30 | Approved alternative: 667-EEU-FR1J151
C10 | 750pF | 0805 | 81-GRM2165C1H751JA | Murata | GRM2165C1H751JA01D | 30 |  | 30
C11 | 1uF 25V X7R | 0805 | 810-C2012X7R1E105K | TDK | C2012X7R1E105K125AB | 30 |  | 30
C12 | 10uF | 0805 | 81-GRM21BR61E106MA3L | Murata | GRM21BR61E106MA73L | 30 |  | 30
C13 | 1uF 25V X7R | 0805 | 810-C2012X7R1E105K | TDK | C2012X7R1E105K125AB | 30 |  | 30
C14 | NF | 0805 | - |  |  | 0
C15 | 100nF | 0805 | 710-885012207072 | Wurth Electronics | 885012207072 | 30 |  | 30
C16 | 100nF | 0805 | 710-885012207072 | Wurth Electronics | 885012207072 | 30 |  | 30
C17 | 100nF | 0805 | 710-885012207072 | Wurth Electronics | 885012207072 | 30 |  | 30
C18 | 10nF | 0805 | 710-885012207092 | Wurth Electronics | 885012207092 | 30 |  | 30
C19 | NF | 0805 | - |  |  | 0
C2 | 2.2uF | 1206 | 81-GRM31CR72A225KA3L | Murata | GRM31CR72A225KA73L | 30 |  | 30
C20 | 39pF | 0805 | 581-08055A390J | AVX | 08055A390JAT2A | 30 |  | 30
C21 | 100nF | 0805 | 710-885012207072 | Wurth Electronics | 885012207072 | 30 |  | 30
C22 | NF | 0805 | - |  |  | 0
C23 | 10nF | 0805 | 710-885012207092 | Wurth Electronics | 885012207092 | 30 |  | 30
C24 | 39pF | 0805 | 581-08055A390J | AVX | 08055A390JAT2A | 30 | 10 | 20
C25 | NF | 0805 | - |  |  | 0
C26 | NF | 0805 | - |  |  | 0
C27 | NF | 0805 | - |  |  | 0
C28 | NF | 0805 | - |  |  | 0
C29 | 10nF | 0805 | 710-885012207092 | Wurth Electronics | 885012207092 | 30 |  | 30
C3 | NF | 0805 | - |  |  | 0
C4 | 1uF | 0805 | 810-C2012X7R1E105K | TDK | C2012X7R1E105K125AB | 30 | 40
C5 | 1uF | 0805 | 810-C2012X7R1E105K | TDK | C2012X7R1E105K125AB | 30 | 40
C6 | 1uF 25V X7R | 0805 | 810-C2012X7R1E105K | TDK | C2012X7R1E105K125AB | 30 |  | 30
C7 | 1uF 25V X7R | 0805 | 810-C2012X7R1E105K | TDK | C2012X7R1E105K125AB | 30 |  | 30
C8 | 10nF | 0805 | 710-885012207092 | Wurth Electronics | 885012207092 | 30 |  | 30
C9 | 68pF | 0805 | 581-08051A680F | AVX | 08051A680FAT2A | 30 |  | 30
D1 | NF | SMC | - |  |  | 0
D10 | RED | 0805 | 859-LTST-C171KRKT | Lite-On | LTST-C171KRKT | 30 | 5 | 25
D11 | BLUE | 0805 | 859-LTST-C170TBKT | Lite-On | LTST-C170TBKT | 30 | 5 | 25
D12 | GREEN | 0805 | 859-LTST-C171GKT | Lite-On | LTST-C171GKT | 30 | 5 | 25
D13 | NF | DO-214AC | - |  |  | 0
D14 | NF | DO-214AC | - |  |  | 0
D15 | NF | DO-214AC | - |  |  | 0
D16 | NF | DO-214AC | - |  |  | 0
D17 | NF | DO-214AC | - |  |  | 0
D18 | NF | DO-214AC | - |  |  | 0
D19 | 3V | SOT-23 | 863-BZX84C3V0LT1G | ON Semiconductor | BZX84C3V0LT1G | 30 |  | 30
D2 | NF | SMC | - |  |  | 0
D3 | NF | SMC | - |  |  | 0
D4 | NF | SMC | - |  |  | 0
D5 | TVS | SMB | 512-SMBJ64CA | Fairchild Semiconductor | SMBJ64CA | 30 |  | 30
D6 | BAV99 | SOT-23 | 863-BAV99LT1G | ON Semiconductor | BAV99LT1G | 30 |  | 30
D7 | NF | SOT-23 | - |  |  | 0
D8 | TVS 12V | DO-214AC | 581-SMAJ12CA | AVX | SMAJ12CA | 30 |  | 30
D9 | TVS 12V | DO-214AC | 581-SMAJ12CA | AVX | SMAJ12CA | 30 |  | 30
F1 | 8A | Fuseholder_5x20_Schurter | 693-0751.0062 | Schurter | 751.0062 | 60 |  | 60
L1 | 220uH 1.57R | INDUCTOR_SDR0604 | 652-SDR0604-221KL | Bourns | SDR0604-221KL | 30 | 5 | 25
P1 | BATT | 5.08mm_2way | 710-691311500102 | Wurth Electronics | 691311500102 | 30 |  | 30
P2 | MOTOR | 5.08mm_2way | 710-691311500102 | Wurth Electronics | 691311500102 | 30 |  | 30
P3 | NF | 5.08mm_2way | - |  |  | 0
P4 | AUX_A | 3.5mm_8way | 649-220107-C081A01LF | FCI / Amphenol | 20020107-C081A01LF | 10 |  | 10
P5 | AUX_B | 3.5mm_5way | 649-220107-C051A01LF | FCI / Amphenol | 20020107-C051A01LF | 10 |  | 10
P6 | COMMS | 3.5mm_3way | 571-796694-3 | TC / AMP | 796694-3 | 30 |  | 30
P7 | ISP | CON_02X05_1.27mm | 649-202112100010C4LF | FCI / Amphenol | 20021121-00010C4LF | 30 |  | 30
Q1 | IPD35N10S3L-26 | TO-252 | 726-IPD35N10S3L26 | Infineon | IPD35N10S3L-26 | 30 |  | 30
Q2 | IPD35N10S3L-26 | TO-252 | 726-IPD35N10S3L26 | Infineon | IPD35N10S3L-26 | 30 |  | 30
Q3 | IPD35N10S3L-26 | TO-252 | 726-IPD35N10S3L26 | Infineon | IPD35N10S3L-26 | 30 |  | 30
Q4 | IPD35N10S3L-26 | TO-252 | 726-IPD35N10S3L26 | Infineon | IPD35N10S3L-26 | 30 |  | 30
Q5 | MMUN2211LT1G | SOT-23 | 863-MMUN2211LT1G | ON Semiconductor | MMUN2211LT1G | 30 |  | 30
Q6 | MMUN2211LT1G | SOT-23 | 863-MMUN2211LT1G | ON Semiconductor | MMUN2211LT1G | 30 |  | 30
R1 | 100R | 0805 | 755-ESR10EZPJ101 | ROHM | ESR10EZPJ101 | 30 | 30
R10 | NF | 0805 | - |  |  | 0
R11 | 0R | 0805 | 71-CRCW0805-0-E3 | Vishay | CRCW08050000Z0EA | 30 | 40
R12 | 140k | 0805 | 71-CRCW0805-140K-E3 | Vishay | CRCW0805140KFKEA | 30 |  | 30
R13 | 10k | 0805 | 71-CRCW0805-10K-E3 | Vishay | CRCW080510K0FKEA | 30 |  | 30
R14 | NF | 0805 | - |  |  | 0
R15 | 0R | 0805 | 71-CRCW0805-0-E3 | Vishay | CRCW08050000Z0EA | 30 | 40
R16 | 1k | 0805 | 71-CRCW0805-1.0K-E3 | Vishay | CRCW08051K00FKEA | 30 |  | 30
R17 | 0R | 0805 | 71-CRCW0805-0-E3 | Vishay | CRCW08050000Z0EA | 30 |  | 30
R18 | 47k | 0805 | 71-CRCW0805-47K-E3 | Vishay | CRCW080547K0FKEA | 30 |  | 30
R19 | 47k | 0805 | 71-CRCW0805-47K-E3 | Vishay | CRCW080547K0FKEA | 30 |  | 30
R2 | 100R | 0805 | 755-ESR10EZPJ101 | ROHM | ESR10EZPJ101 | 30 | 30
R20 | NF | 0805 | - |  |  | 0
R21 | NF | 0805 | - |  |  | 0
R22 | NF | 0805 | - |  |  | 0
R23 | NF | 0805 | - |  |  | 0
R24 | 1k8 | 0805 | 71-CRCW0805-1.8K-E3 | Vishay | CRCW08051K80FKEA | 30 |  | 30
R25 | 1k8 | 0805 | 71-CRCW0805-1.8K-E3 | Vishay | CRCW08051K80FKEA | 30 |  | 30
R26 | 1k8 | 0805 | 71-CRCW0805-1.8K-E3 | Vishay | CRCW08051K80FKEA | 30 |  | 30
R27 | 120k | 0805 | 71-CRCW0805120KFKEA | Vishay | CRCW0805120KFKEA | 30 |  | 30
R28 | 10k | 0805 | 71-CRCW0805-10K-E3 | Vishay | CRCW080510K0FKEA | 30 |  | 30
R29 | 10k | 0805 | 71-CRCW0805-10K-E3 | Vishay | CRCW080510K0FKEA | 30 |  | 30
R3 | NF | 0805 | - |  |  | 0
R4 | NF | 0805 | - |  |  | 0
R5 | 97.6k | 0805 | 71-CRCW0805-97.6K-E3 | Vishay | CRCW080597K6FKEA | 30 |  | 30
R6 | 0.01R 1W | 2512 | 756-LRMAM2512R01FT4 | TT Electronics | LRMAM2512-R01FT4 | 30 |  | 30
R7 | 158k | 0805 | 71-CRCW0805158KFKEA | Vishay | CRCW0805158KFKEA | 30 |  | 30
R8 | 100R | 0805 | 755-ESR10EZPJ101 | ROHM | ESR10EZPJ101 | 30 | 30
R9 | 100R | 0805 | 755-ESR10EZPJ101 | ROHM | ESR10EZPJ101 | 30 | 30
TH1 | NTCS0805E3103JMT | 0805 | 594-2381-615-53103 | Vishay | NTCS0805E3103JMT | 30 |  | 30
U1 | LPC1114FDH28/102 | TSSOP-28 | 771-LPC1114FDH28/102 | NXP | LPC1114FDH28/102:5 | 30 |  | 30
U2 | TPS54061 | VSON8 | 595-TPS54061DRBR | Texas Instruments | TPS54061DRBR | 30 |  | 30
U3 | MIC5205-3.3YM5 | SOT-23-5 | 998-MIC5205-3.3YM5TR | Microchip | MIC5205-3.3YM5-TR | 30 | 5 | 25
U4 | ST_CS70 | TSSOP-8 | 511-CS70P | STMicroelectronics | CS70P | 30 |  | 30
U5 | MIC4605-1YM | SOIC-8 | 998-MIC4605-1YM | Microchip | MIC4605-1YM | 30 |  | 30
U6 | MIC4605-1YM | SOIC-8 | 998-MIC4605-1YM | Microchip | MIC4605-1YM | 30 |  | 30
U7 | MAX3485 | SOIC-8 | 700-MAX3485CSA | Maxim Integrated | MAX3485CSA+ | 30 |  | 30
Y1 | 12MHz 20pF | Crystal_FOX_HC | 559-FOXSDLF/120R-20 | Fox | FOXSDLF/120R-20/TR | 30 |  | 30
F1a | 8A | Fuse | 530-5ST8-R | Bel | 5ST 8-R | 30 |  | 30
P1a | BATT | 5.08mm_2way | 571-284047-2 | TE / AMP | 284047-2 | 30 |  | 30
P2a | MOTOR | 5.08mm_2way | 571-284047-2 | TE / AMP | 284047-2 | 30 |  | 30
P4a | NF | 3.5mm_8way | 538-39503-2008 |  |  | 0
P5a | NF | 3.5mm_5way | 538-39500-0005 |  |  | 0
P6a | COMMS | 3.5mm_3way | 538-39503-2003 | Molex | 39503-2003 | 30 |  | 30

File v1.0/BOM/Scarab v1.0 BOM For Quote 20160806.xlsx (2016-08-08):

Scarab v1.0 BOM 20160806
 |  |  |  |  | Build qty | 40
 | Preferred parts listed with Mouser order number
 | Substitutions accepted with prior approval
 | Do not quote no-fit parts (marked NF)
Reference | Value | Footprint | Mouser No. | Manufacturer | Manf. Part No. | Total Reqd | On Hand | Qty To Purchase
C1 | 150uF | C_Radial_D10_L20_P | 647-UPW1J151MPD | Nichicon | UPW1J151MPD | 40 |  | 40 | Approved alternative: 667-EEU-FR1J151
C10 | 750pF | 0805 | 81-GRM2165C1H751JA | Murata | GRM2165C1H751JA01D | 40 |  | 40
C11 | 1uF 25V X7R | 0805 | 810-C2012X7R1E105K | TDK | C2012X7R1E105K125AB | 40 |  | 40
C12 | 10uF | 0805 | 81-GRM21BR61E106MA3L | Murata | GRM21BR61E106MA73L | 40 |  | 40
C13 | 1uF 25V X7R | 0805 | 810-C2012X7R1E105K | TDK | C2012X7R1E105K125AB | 40 |  | 40
C14 | NF | 0805 | - |  |  | 0
C15 | 100nF | 0805 | 710-885012207072 | Wurth Electronics | 885012207072 | 40 |  | 40
C16 | 100nF | 0805 | 710-885012207072 | Wurth Electronics | 885012207072 | 40 |  | 40
C17 | 100nF | 0805 | 710-885012207072 | Wurth Electronics | 885012207072 | 40 |  | 40
C18 | 10nF | 0805 | 710-885012207092 | Wurth Electronics | 885012207092 | 40 |  | 40
C19 | NF | 0805 | - |  |  | 0
C2 | 2.2uF | 1206 | 81-GRM31CR72A225KA3L | Murata | GRM31CR72A225KA73L | 40 |  | 40
C20 | 39pF | 0805 | 581-08055A390J | AVX | 08055A390JAT2A | 40 |  | 40
C21 | 100nF | 0805 | 710-885012207072 | Wurth Electronics | 885012207072 | 40 |  | 40
C22 | NF | 0805 | - |  |  | 0
C23 | 10nF | 0805 | 710-885012207092 | Wurth Electronics | 885012207092 | 40 |  | 40
C24 | 39pF | 0805 | 581-08055A390J | AVX | 08055A390JAT2A | 40 | 10 | 30
C25 | NF | 0805 | - |  |  | 0
C26 | NF | 0805 | - |  |  | 0
C27 | NF | 0805 | - |  |  | 0
C28 | NF | 0805 | - |  |  | 0
C29 | 10nF | 0805 | 710-885012207092 | Wurth Electronics | 885012207092 | 40 |  | 40
C3 | NF | 0805 | - |  |  | 0
C4 | 1uF | 0805 | 810-C2012X7R1E105K | TDK | C2012X7R1E105K125AB | 40 | 40 | 0
C5 | 1uF | 0805 | 810-C2012X7R1E105K | TDK | C2012X7R1E105K125AB | 40 | 40 | 0
C6 | 1uF 25V X7R | 0805 | 810-C2012X7R1E105K | TDK | C2012X7R1E105K125AB | 40 |  | 40
C7 | 1uF 25V X7R | 0805 | 810-C2012X7R1E105K | TDK | C2012X7R1E105K125AB | 40 |  | 40
C8 | 10nF | 0805 | 710-885012207092 | Wurth Electronics | 885012207092 | 40 |  | 40
C9 | 68pF | 0805 | 581-08051A680F | AVX | 08051A680FAT2A | 40 |  | 40
D1 | NF | SMC | - |  |  | 0
D10 | RED | 0805 | 859-LTST-C171KRKT | Lite-On | LTST-C171KRKT | 40 | 5 | 35
D11 | BLUE | 0805 | 859-LTST-C170TBKT | Lite-On | LTST-C170TBKT | 40 | 5 | 35
D12 | GREEN | 0805 | 859-LTST-C171GKT | Lite-On | LTST-C171GKT | 40 | 5 | 35
D13 | NF | DO-214AC | - |  |  | 0
D14 | NF | DO-214AC | - |  |  | 0
D15 | NF | DO-214AC | - |  |  | 0
D16 | NF | DO-214AC | - |  |  | 0
D17 | NF | DO-214AC | - |  |  | 0
D18 | NF | DO-214AC | - |  |  | 0
D19 | 3V | SOT-23 | 863-BZX84C3V0LT1G | ON Semiconductor | BZX84C3V0LT1G | 40 |  | 40
D2 | NF | SMC | - |  |  | 0
D3 | NF | SMC | - |  |  | 0
D4 | NF | SMC | - |  |  | 0
D5 | TVS | SMB | 512-SMBJ64CA | Fairchild Semiconductor | SMBJ64CA | 40 |  | 40
D6 | BAV99 | SOT-23 | 863-BAV99LT1G | ON Semiconductor | BAV99LT1G | 40 |  | 40
D7 | NF | SOT-23 | - |  |  | 0
D8 | TVS 12V | DO-214AC | 581-SMAJ12CA | AVX | SMAJ12CA | 40 |  | 40
D9 | TVS 12V | DO-214AC | 581-SMAJ12CA | AVX | SMAJ12CA | 40 |  | 40
F1 | 8A | Fuseholder_5x20_Schurter | 693-0751.0062 | Schurter | 751.0062 | 80 |  | 80
L1 | 220uH 1.57R | INDUCTOR_SDR0604 | 652-SDR0604-221KL | Bourns | SDR0604-221KL | 40 | 5 | 35
P1 | BATT | 5.08mm_2way | 710-691311500102 | Wurth Electronics | 691311500102 | 40 |  | 40
P2 | MOTOR | 5.08mm_2way | 710-691311500102 | Wurth Electronics | 691311500102 | 40 |  | 40
P3 | NF | 5.08mm_2way | - |  |  | 0
P4 | AUX_A | 3.5mm_8way | 649-220107-C081A01LF | FCI / Amphenol | 20020107-C081A01LF | 10 |  | 10
P5 | AUX_B | 3.5mm_5way | 649-220107-C051A01LF | FCI / Amphenol | 20020107-C051A01LF | 10 |  | 10
P6 | COMMS | 3.5mm_3way | 571-796694-3 | TC / AMP | 796694-3 | 40 |  | 40
P7 | ISP | CON_02X05_1.27mm | 649-202112100010C4LF | FCI / Amphenol | 20021121-00010C4LF | 40 |  | 40
Q1 | IPD35N10S3L-26 | TO-252 | 726-IPD35N10S3L26 | Infineon | IPD35N10S3L-26 | 40 |  | 40
Q2 | IPD35N10S3L-26 | TO-252 | 726-IPD35N10S3L26 | Infineon | IPD35N10S3L-26 | 40 |  | 40
Q3 | IPD35N10S3L-26 | TO-252 | 726-IPD35N10S3L26 | Infineon | IPD35N10S3L-26 | 40 |  | 40
Q4 | IPD35N10S3L-26 | TO-252 | 726-IPD35N10S3L26 | Infineon | IPD35N10S3L-26 | 40 |  | 40
Q5 | MMUN2211LT1G | SOT-23 | 863-MMUN2211LT1G | ON Semiconductor | MMUN2211LT1G | 40 |  | 40
Q6 | MMUN2211LT1G | SOT-23 | 863-MMUN2211LT1G | ON Semiconductor | MMUN2211LT1G | 40 |  | 40
R1 | 100R | 0805 | 755-ESR10EZPJ101 | ROHM | ESR10EZPJ101 | 40 | 40 | 0
R10 | NF | 0805 | - |  |  | 0
R11 | 0R | 0805 | 71-CRCW0805-0-E3 | Vishay | CRCW08050000Z0EA | 40 | 40 | 0
R12 | 140k | 0805 | 71-CRCW0805-140K-E3 | Vishay | CRCW0805140KFKEA | 40 |  | 40
R13 | 10k | 0805 | 71-CRCW0805-10K-E3 | Vishay | CRCW080510K0FKEA | 40 |  | 40
R14 | NF | 0805 | - |  |  | 0
R15 | 0R | 0805 | 71-CRCW0805-0-E3 | Vishay | CRCW08050000Z0EA | 40 | 40 | 0
R16 | 1k | 0805 | 71-CRCW0805-1.0K-E3 | Vishay | CRCW08051K00FKEA | 40 |  | 40
R17 | 0R | 0805 | 71-CRCW0805-0-E3 | Vishay | CRCW08050000Z0EA | 40 |  | 40
R18 | 47k | 0805 | 71-CRCW0805-47K-E3 | Vishay | CRCW080547K0FKEA | 40 |  | 40
R19 | 47k | 0805 | 71-CRCW0805-47K-E3 | Vishay | CRCW080547K0FKEA | 40 |  | 40
R2 | 100R | 0805 | 755-ESR10EZPJ101 | ROHM | ESR10EZPJ101 | 40 | 40 | 0
R20 | NF | 0805 | - |  |  | 0
R21 | NF | 0805 | - |  |  | 0
R22 | NF | 0805 | - |  |  | 0
R23 | NF | 0805 | - |  |  | 0
R24 | 1k8 | 0805 | 71-CRCW0805-1.8K-E3 | Vishay | CRCW08051K80FKEA | 40 |  | 40
R25 | 1k8 | 0805 | 71-CRCW0805-1.8K-E3 | Vishay | CRCW08051K80FKEA | 40 |  | 40
R26 | 1k8 | 0805 | 71-CRCW0805-1.8K-E3 | Vishay | CRCW08051K80FKEA | 40 |  | 40
R27 | 120k | 0805 | 71-CRCW0805120KFKEA | Vishay | CRCW0805120KFKEA | 40 |  | 40
R28 | 10k | 0805 | 71-CRCW0805-10K-E3 | Vishay | CRCW080510K0FKEA | 40 |  | 40
R29 | 10k | 0805 | 71-CRCW0805-10K-E3 | Vishay | CRCW080510K0FKEA | 40 |  | 40
R3 | NF | 0805 | - |  |  | 0
R4 | NF | 0805 | - |  |  | 0
R5 | 97.6k | 0805 | 71-CRCW0805-97.6K-E3 | Vishay | CRCW080597K6FKEA | 40 |  | 40
R6 | 0.01R 1W | 2512 | 756-LRMAM2512R01FT4 | TT Electronics | LRMAM2512-R01FT4 | 40 |  | 40
R7 | 158k | 0805 | 71-CRCW0805158KFKEA | Vishay | CRCW0805158KFKEA | 40 |  | 40
R8 | 100R | 0805 | 755-ESR10EZPJ101 | ROHM | ESR10EZPJ101 | 40 | 40 | 0
R9 | 100R | 0805 | 755-ESR10EZPJ101 | ROHM | ESR10EZPJ101 | 40 | 40 | 0
TH1 | NTCS0805E3103JMT | 0805 | 594-2381-615-53103 | Vishay | NTCS0805E3103JMT | 40 |  | 40
U1 | LPC1114FDH28/102 | TSSOP-28 | 771-LPC1114FDH28/102 | NXP | LPC1114FDH28/102:5 | 40 |  | 40
U2 | TPS54061 | VSON8 | 595-TPS54061DRBR | Texas Instruments | TPS54061DRBR | 40 |  | 40
U3 | MIC5205-3.3YM5 | SOT-23-5 | 998-MIC5205-3.3YM5TR | Microchip | MIC5205-3.3YM5-TR | 40 | 5 | 35
U4 | ST_CS70 | TSSOP-8 | 511-CS70P | STMicroelectronics | CS70P | 40 |  | 40
U5 | MIC4605-1YM | SOIC-8 | 998-MIC4605-1YM | Microchip | MIC4605-1YM | 40 |  | 40
U6 | MIC4605-1YM | SOIC-8 | 998-MIC4605-1YM | Microchip | MIC4605-1YM | 40 |  | 40
U7 | MAX3485 | SOIC-8 | 700-MAX3485CSA | Maxim Integrated | MAX3485CSA+ | 40 |  | 40
Y1 | 12MHz 20pF | Crystal_FOX_HC | 559-FOXSDLF/120R-20 | Fox | FOXSDLF/120R-20/TR | 40 |  | 40
F1a | 8A | Fuse | 530-5ST8-R | Bel | 5ST 8-R | 40 |  | 40
P1a | BATT | 5.08mm_2way | 571-284047-2 | TE / AMP | 284047-2 | 40 |  | 40
P2a | MOTOR | 5.08mm_2way | 571-284047-2 | TE / AMP | 284047-2 | 40 |  | 40
P4a | NF | 3.5mm_8way | 538-39503-2008 |  |  | 0
P5a | NF | 3.5mm_5way | 538-39500-0005 |  |  | 0
P6a | COMMS | 3.5mm_3way | 538-39503-2003 | Molex | 39503-2003 | 40 |  | 40

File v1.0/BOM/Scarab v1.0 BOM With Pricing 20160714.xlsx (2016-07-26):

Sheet: Sheet1
Scarab v1.0 BOM 20160714
 | Preferred parts listed with Mouser order number
 | Substitutions accepted with prior approval
 | Do not quote no-fit parts (marked NF)
Reference | Value | Footprint | Mouser No. | Price | Manufacturer | Manf. Part No. | Mating Part | Mating Part Price
C1 | 150uF | C_Radial_D10_L20_P | 647-UPW1J151MPD | 0.592 | Nichicon | UPW1J151MPD
C10 | 750pF | 0805 | 81-GRM2165C1H751JA | 0.122 | Murata | GRM2165C1H751JA01D
C11 | 1uF 25V X7R | 0805 | 810-C2012X7R1E105K | 0.082 | TDK | C2012X7R1E105K125AB
C12 | 10uF | 0805 | 81-GRM21BR61E106MA3L | 0.138 | Murata | GRM21BR61E106MA73L
C13 | 1uF 25V X7R | 0805 | 810-C2012X7R1E105K | 0.082 | TDK | C2012X7R1E105K125AB
C14 | NF | 0805 | - | 0
C15 | 100nF | 0805 | 710-885012207072 | 0.08 | Wurth Electronics | 885012207072
C16 | 100nF | 0805 | 710-885012207072 | 0.08 | Wurth Electronics | 885012207072
C17 | 100nF | 0805 | 710-885012207072 | 0.08 | Wurth Electronics | 885012207072
C18 | 10nF | 0805 | 710-885012207092 | 0.112 | Wurth Electronics | 885012207092
C19 | NF | 0805 | - | 0
C2 | 2.2uF | 1206 | 81-GRM31CR72A225KA3L | 0.534 | Murata | GRM31CR72A225KA73L
C20 | 39pF | 0805 | 581-08055A390J | 0.16 | AVX | 08055A390JAT2A
C21 | 100nF | 0805 | 710-885012207072 | 0.08 | Wurth Electronics | 885012207072
C22 | NF | 0805 | - | 0
C23 | 10nF | 0805 | 710-885012207092 | 0.112 | Wurth Electronics | 885012207092
C24 | 39pF | 0805 | 581-08055A390J | 0.16 | AVX | 08055A390JAT2A
C25 | NF | 0805 | - | 0
C26 | NF | 0805 | - | 0
C27 | NF | 0805 | - | 0
C28 | NF | 0805 | - | 0
C29 | 10nF | 0805 | 710-885012207092 | 0.112 | Wurth Electronics | 885012207092
C3 | NF | 0805 | - | 0
C4 | 1uF | 0805 | 810-C2012X7R1E105K | 0.082 | TDK | C2012X7R1E105K125AB
C5 | 1uF | 0805 | 810-C2012X7R1E105K | 0.082 | TDK | C2012X7R1E105K125AB
C6 | 1uF 25V X7R | 0805 | 810-C2012X7R1E105K | 0.082 | TDK | C2012X7R1E105K125AB
C7 | 1uF 25V X7R | 0805 | 810-C2012X7R1E105K | 0.082 | TDK | C2012X7R1E105K125AB
C8 | 10nF | 0805 | 710-885012207092 | 0.112 | Wurth Electronics | 885012207092
C9 | 68pF | 0805 | 581-08051A680F | 0.16 | AVX | 08051A680FAT2A
D1 | NF | SMC | - | 0
D10 | RED | 0805 | 859-LTST-C171KRKT | 0.397 | Lite-On | LTST-C171KRKT
D11 | BLUE | 0805 | 859-LTST-C170TBKT | 0.443 | Lite-On | LTST-C170TBKT
D12 | GREEN | 0805 | 859-LTST-C171GKT | 0.381 | Lite-On | LTST-C171GKT
D13 | NF | DO-214AC | - | 0
D14 | NF | DO-214AC | - | 0
D15 | NF | DO-214AC | - | 0
D16 | NF | DO-214AC | - | 0
D17 | NF | DO-214AC | - | 0
D18 | NF | DO-214AC | - | 0
D19 | 3V | SOT-23 | 863-BZX84C3V0LT1G | 0.2 | ON Semiconductor | BZX84C3V0LT1G
D2 | NF | SMC | - | 0
D3 | NF | SMC | - | 0
D4 | NF | SMC | - | 0
D5 | TVS | SMB | 512-SMBJ64CA | 0.429 | Fairchild Semiconductor | SMBJ64CA
D6 | BAV99 | SOT-23 | 863-BAV99LT1G | 0.17 | ON Semiconductor | BAV99LT1G
D7 | NF | SOT-23 | - | 0
D8 | TVS 12V | DO-214AC | 581-SMAJ12CA | 0.512 | AVX | SMAJ12CA
D9 | TVS 12V | DO-214AC | 581-SMAJ12CA | 0.512 | AVX | SMAJ12CA
F1 | 8A | Fuseholder_5x20_Schurter | 2 x 693-0751.0062 | 0.352 | Schurter | 751.0062 | 530-5ST8-R | 0.323
L1 | 220uH 1.57R | INDUCTOR_SDR0604 | 652-SDR0604-221KL | 0.541 | Bourns | SDR0604-221KL
P1 | BATT | 5.08mm_2way | 710-691311500102 | 0.44 | Wurth Electronics | 691311500102 | 649-202007H021B01LF | 1.13
P2 | MOTOR | 5.08mm_2way | 710-691311500102 | 0.44 | Wurth Electronics | 691311500102 | 649-202007H021B01LF | 1.13
P3 | NF | 5.08mm_2way | - | 0
P4 | AUX_A | 3.5mm_8way | 649-220107-C081A01LF | 1.14 | FCI / Amphenol | 20020107-C081A01LF | 538-39503-2008 | 3.44
P5 | AUX_B | 3.5mm_5way | 649-220107-C051A01LF | 0.842 | FCI / Amphenol | 20020107-C051A01LF | 538-39500-0005 | 2.29
P6 | COMMS | 3.5mm_6way | 649-220107-C061A01LF | 1.01 | FCI / Amphenol | 20020107-C061A01LF | 538-39500-0006 | 2.72
P7 | ISP | CON_02X05_1.27mm | 649-202112100010C4LF | 1.02 | FCI / Amphenol | 20021121-00010C4LF
Q1 | IPD35N10S3L-26 | TO-252 | 726-IPD35N10S3L26 | 1.19 | Infineon | IPD35N10S3L-26
Q2 | IPD35N10S3L-26 | TO-252 | 726-IPD35N10S3L26 | 1.19 | Infineon | IPD35N10S3L-26
Q3 | IPD35N10S3L-26 | TO-252 | 726-IPD35N10S3L26 | 1.19 | Infineon | IPD35N10S3L-26
Q4 | IPD35N10S3L-26 | TO-252 | 726-IPD35N10S3L26 | 1.19 | Infineon | IPD35N10S3L-26
Q5 | MMUN2211LT1G | SOT-23 | 863-MMUN2211LT1G | 0.179 | ON Semiconductor | MMUN2211LT1G
Q6 | MMUN2211LT1G | SOT-23 | 863-MMUN2211LT1G | 0.179 | ON Semiconductor | MMUN2211LT1G
R1 | 0R | 0805 | 71-CRCW0805-0-E3 | 0.067 | Vishay | CRCW08050000Z0EA
R10 | NF | 0805 | - | 0
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

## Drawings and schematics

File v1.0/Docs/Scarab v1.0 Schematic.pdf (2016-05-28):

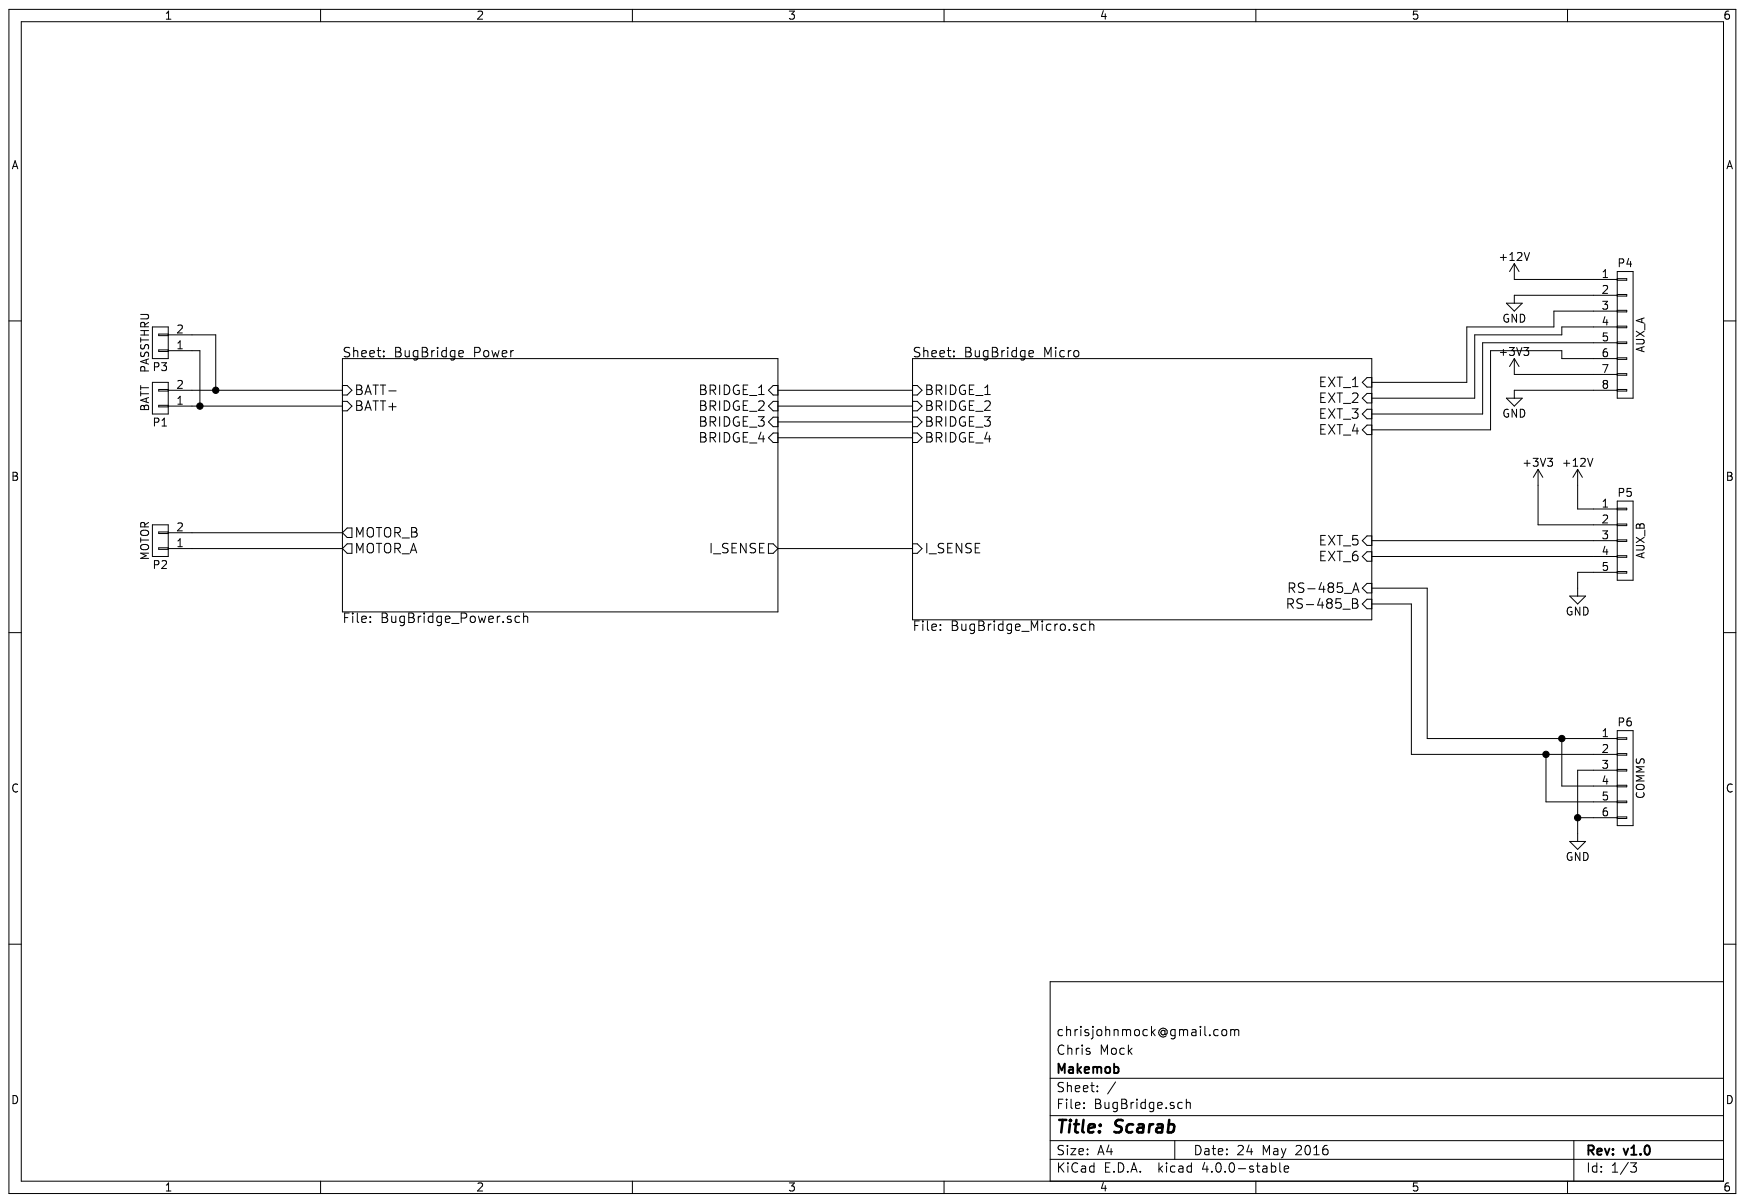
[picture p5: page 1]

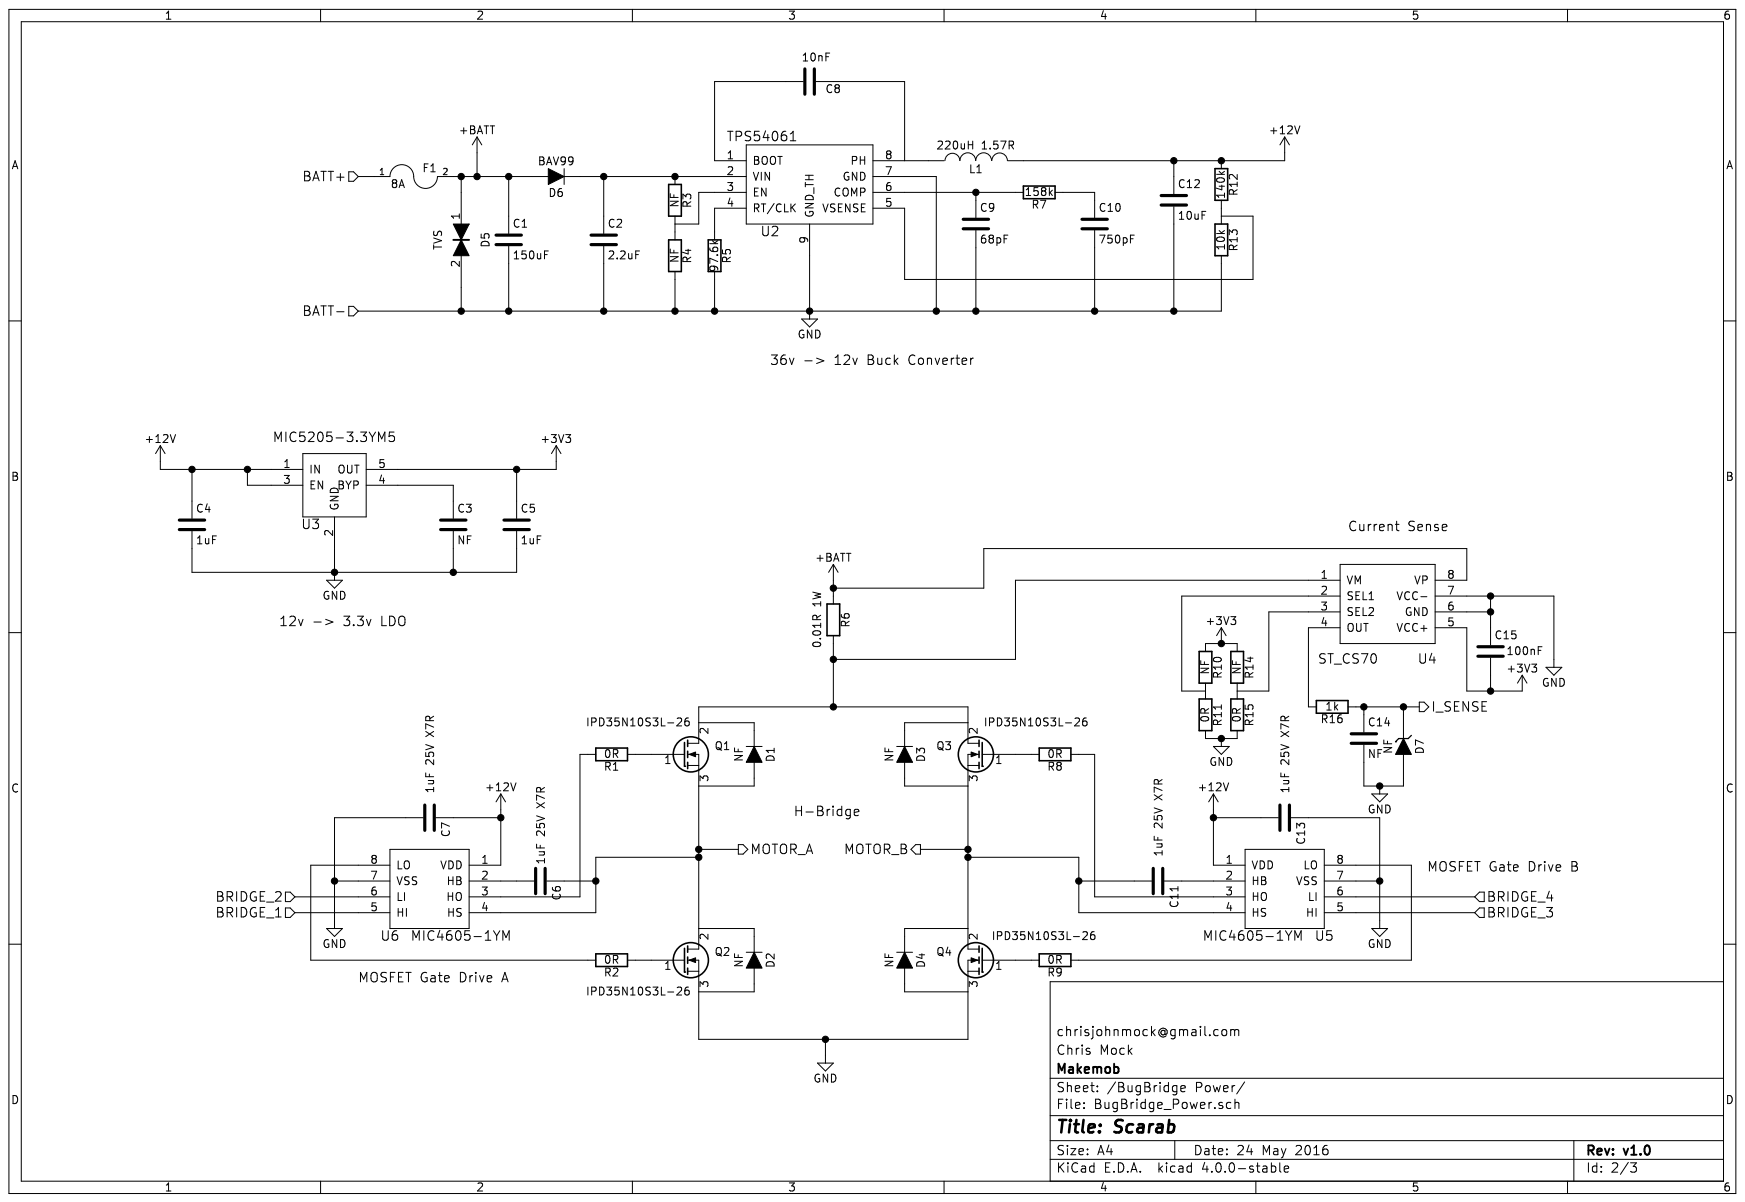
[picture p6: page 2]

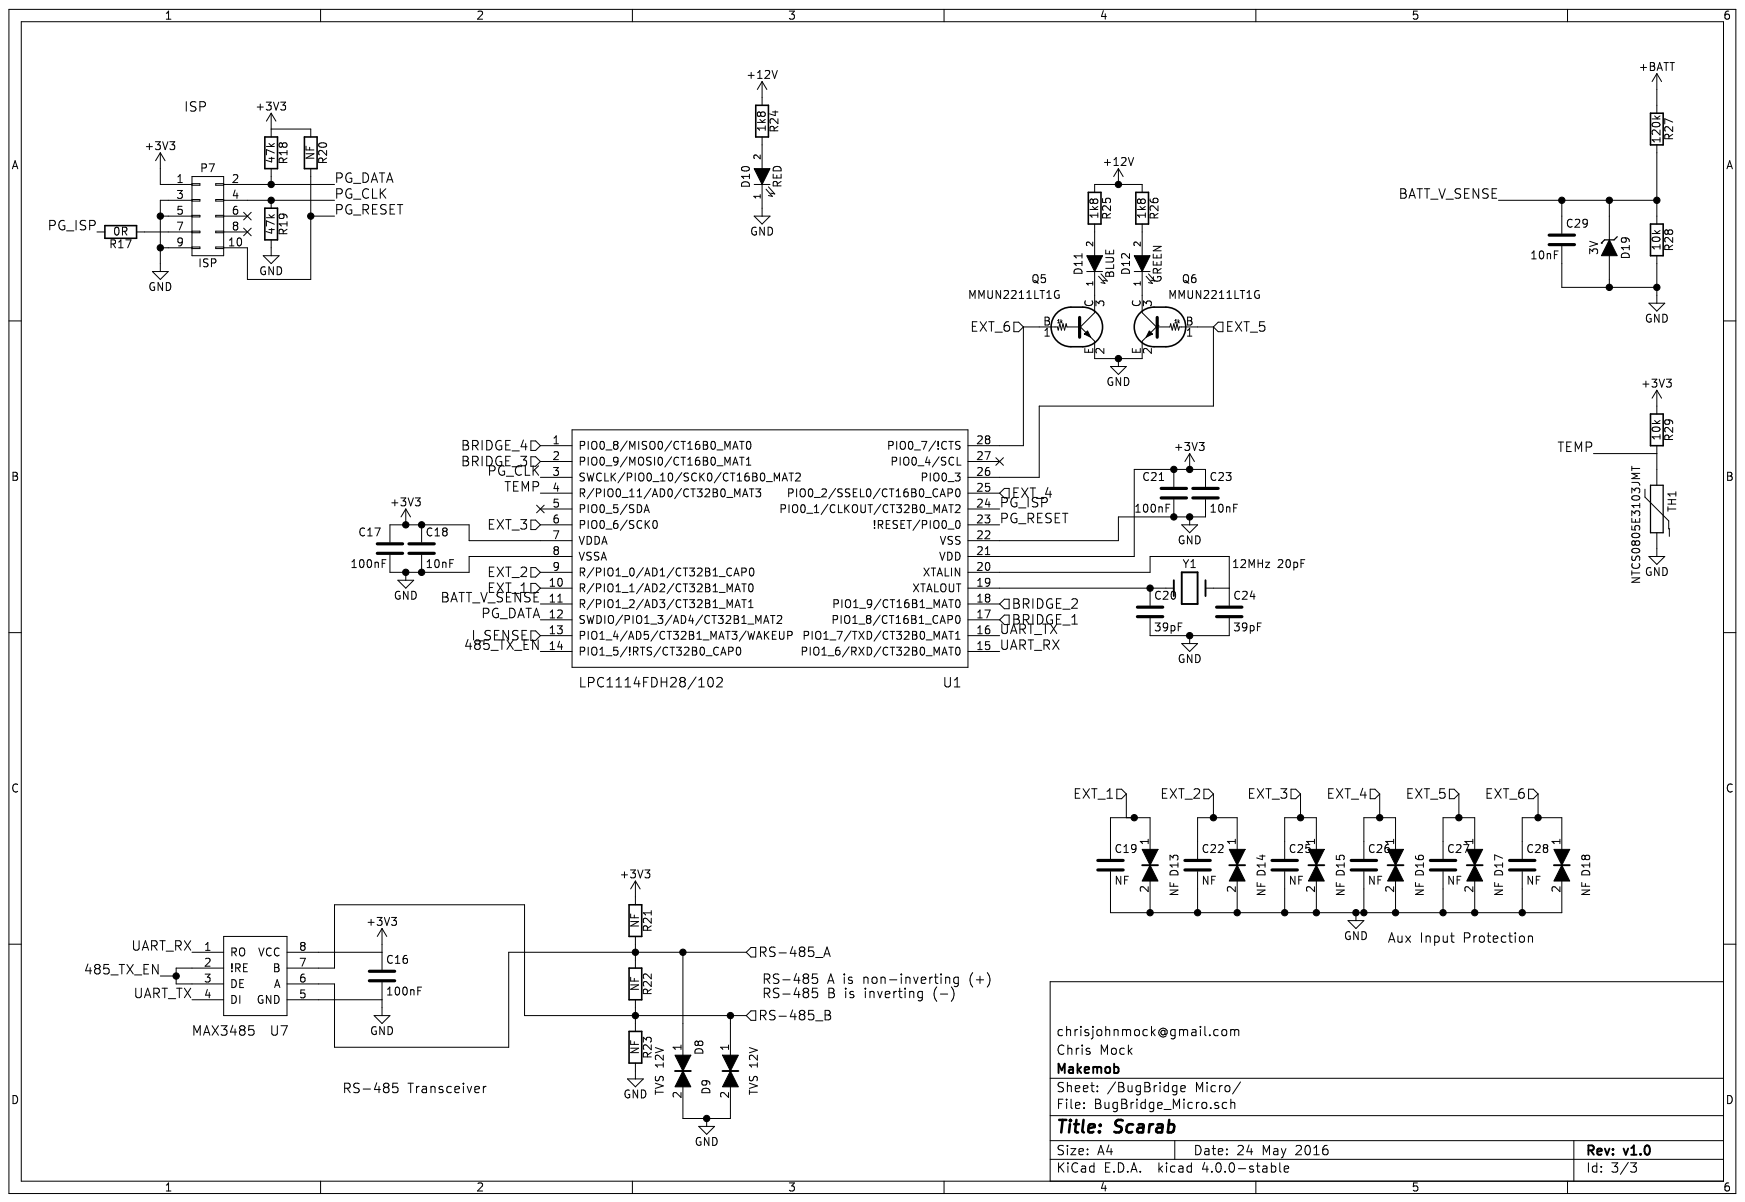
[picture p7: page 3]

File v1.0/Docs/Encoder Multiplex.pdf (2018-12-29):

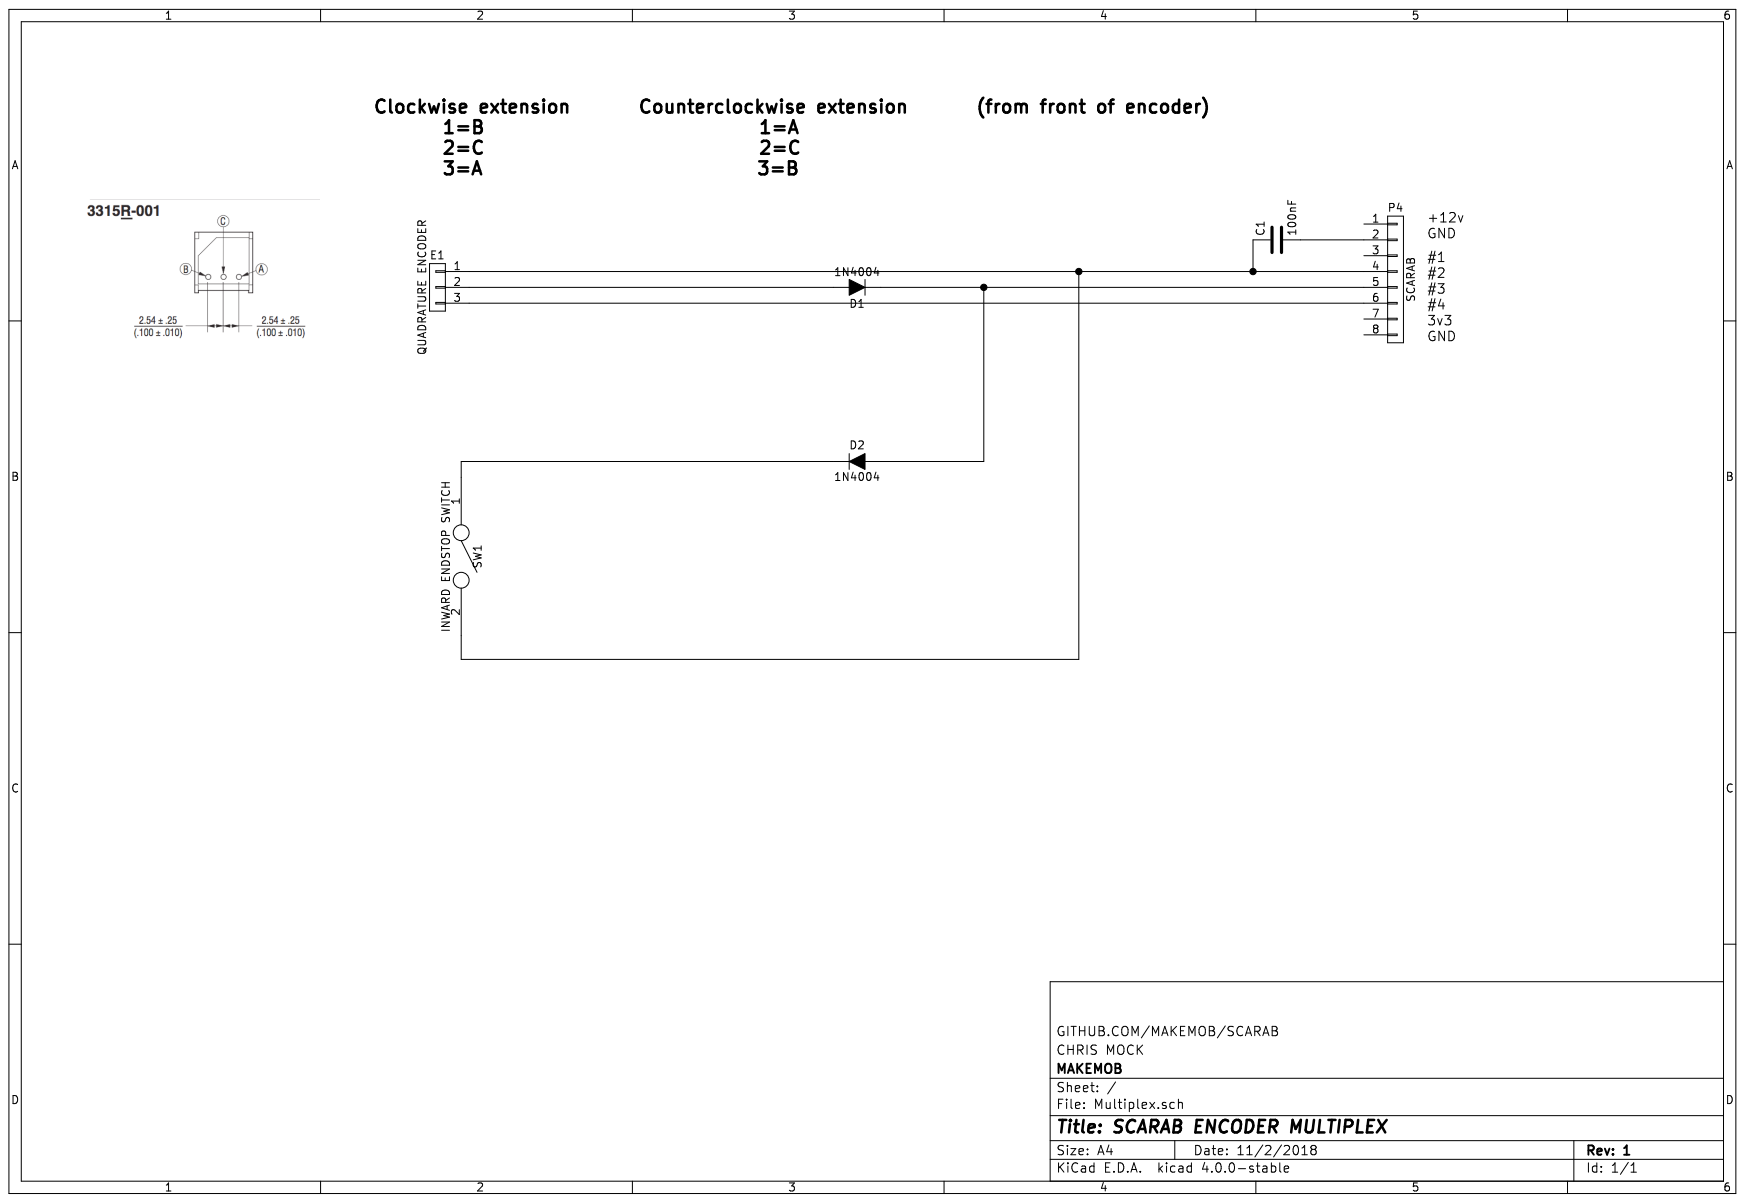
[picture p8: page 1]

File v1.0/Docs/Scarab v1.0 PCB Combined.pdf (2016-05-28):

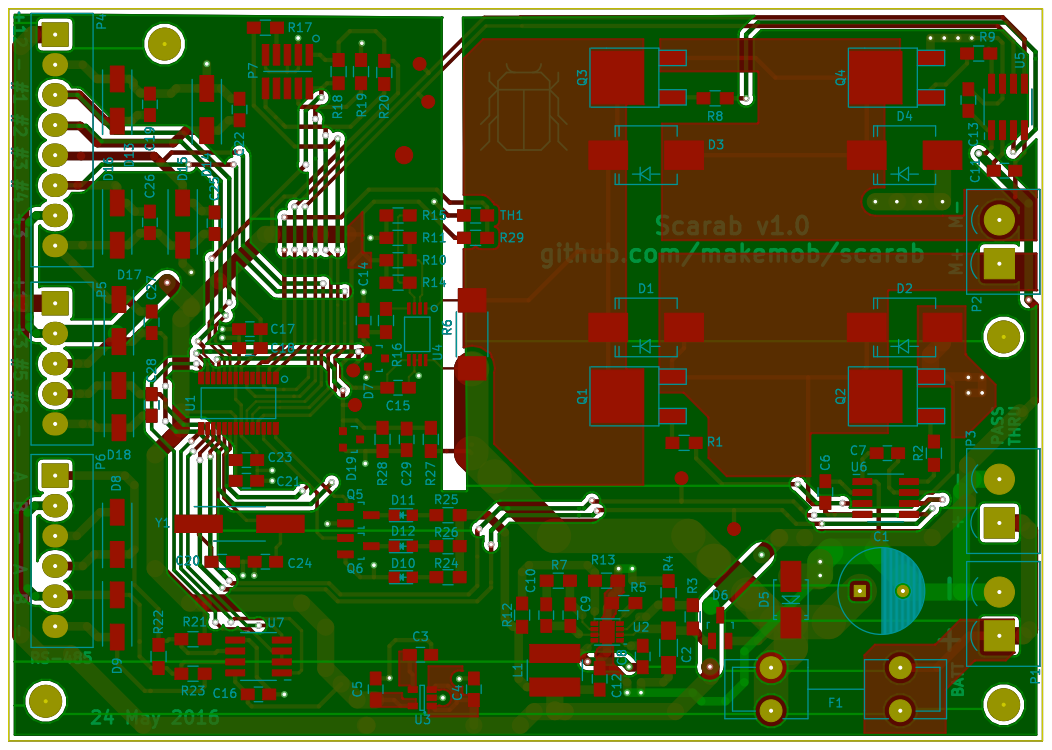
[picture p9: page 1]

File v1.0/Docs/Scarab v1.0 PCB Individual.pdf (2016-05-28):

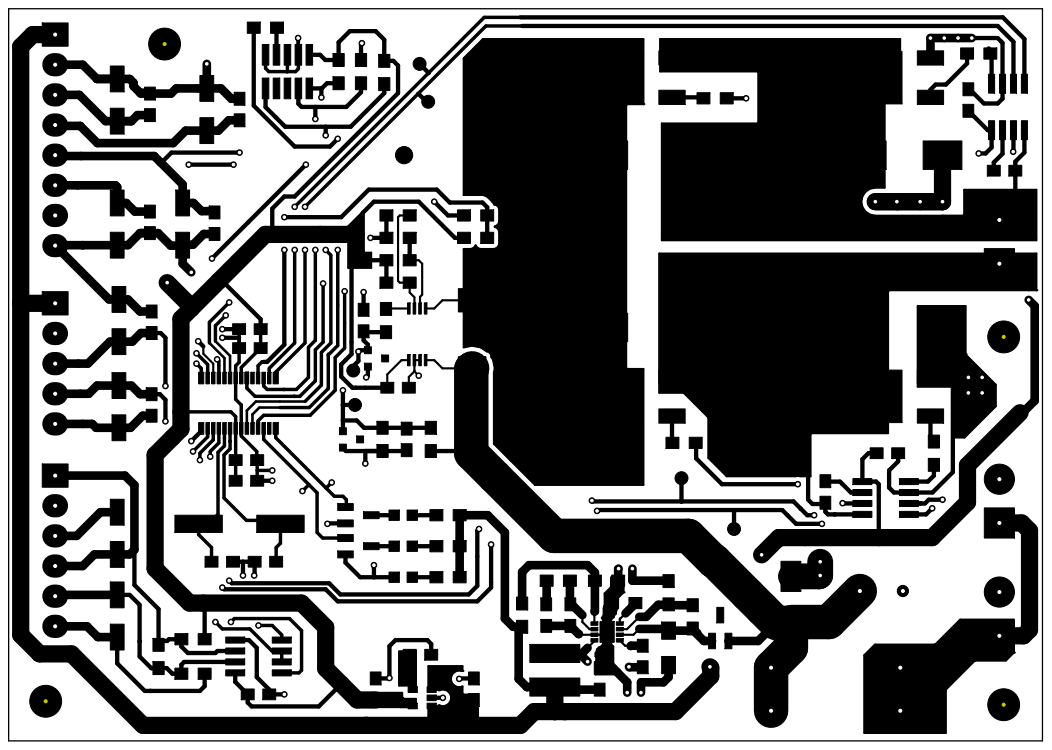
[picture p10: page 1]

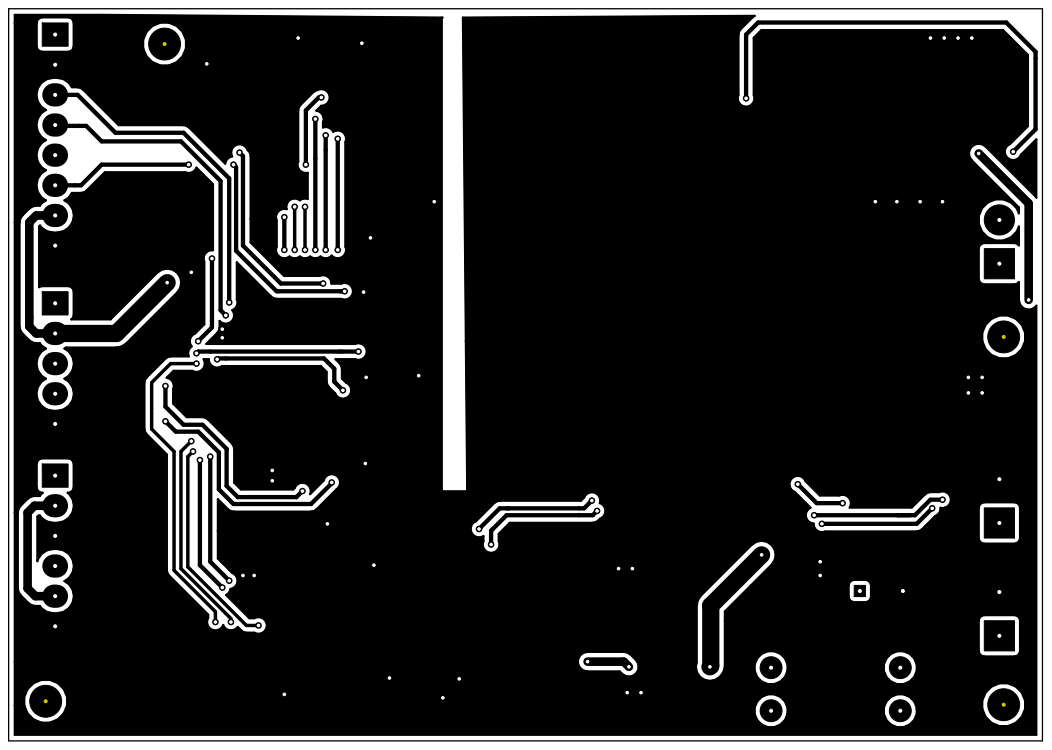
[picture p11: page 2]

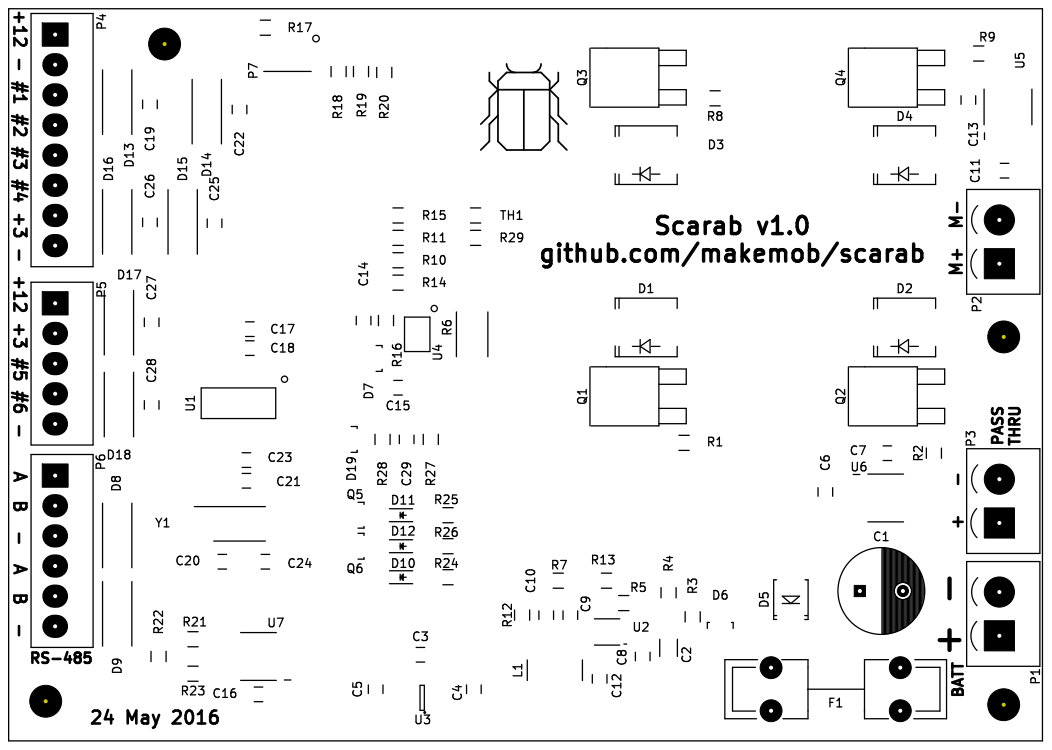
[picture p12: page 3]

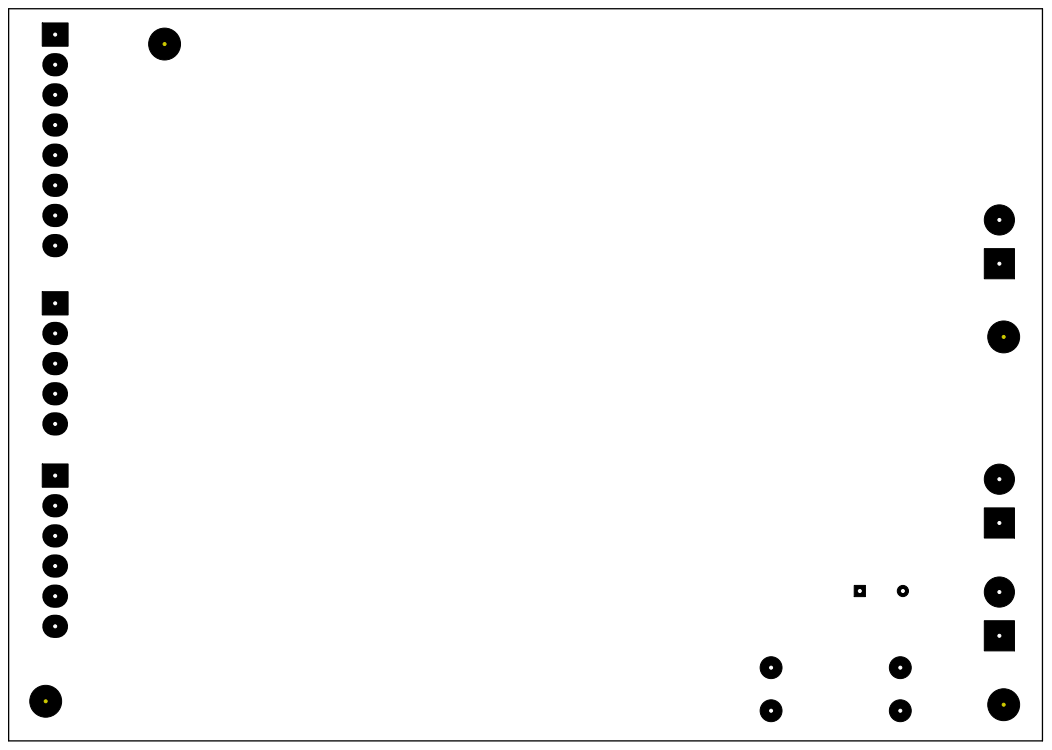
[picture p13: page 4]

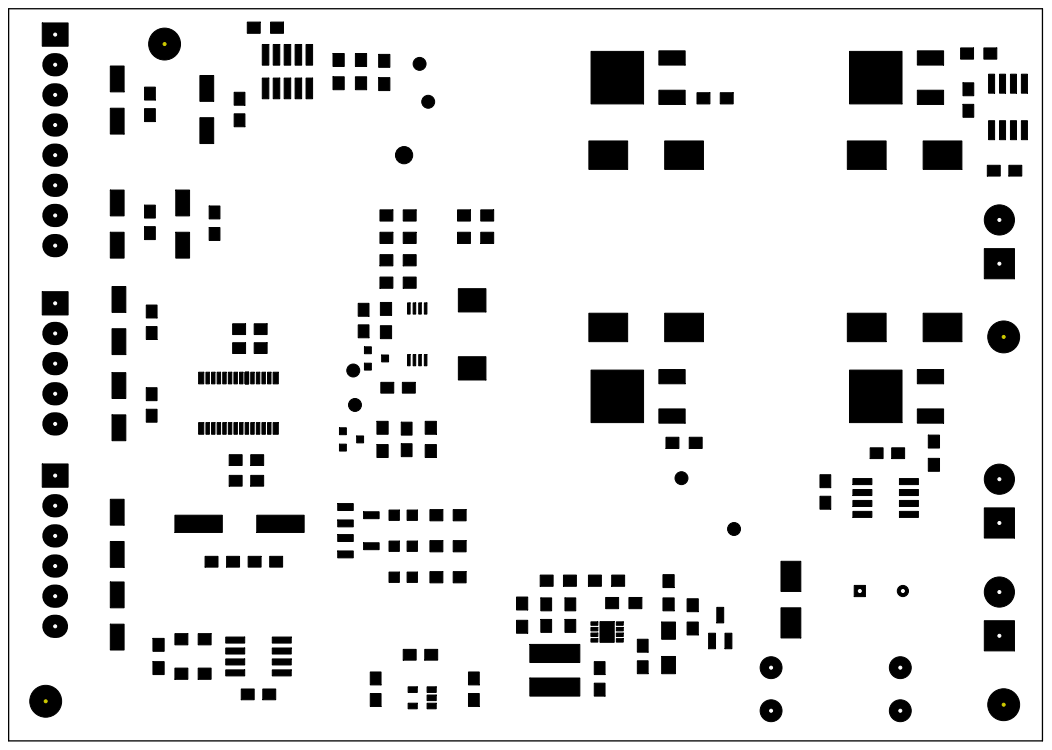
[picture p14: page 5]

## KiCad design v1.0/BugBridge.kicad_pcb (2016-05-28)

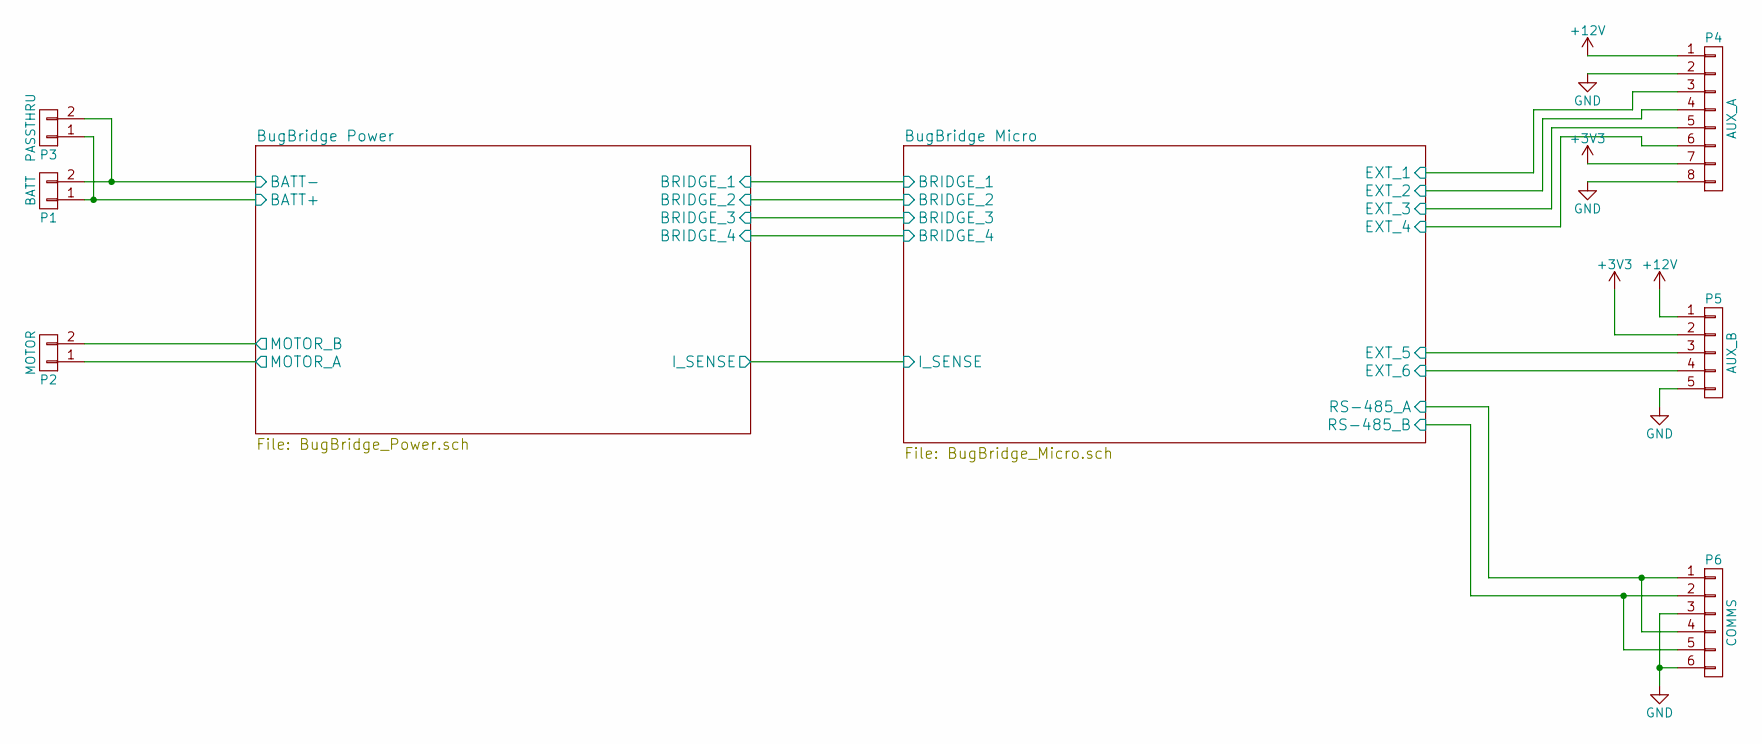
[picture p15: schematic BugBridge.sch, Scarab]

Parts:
P1: BATT; Connector_5.08mm_Pitch_2way
P2: MOTOR; Connector_5.08mm_Pitch_2way
P3: PASSTHRU; Connector_5.08mm_Pitch_2way
P4: AUX_A; Connector_3.5mm_Pitch_8way
P5: AUX_B; Connector_3.5mm_Pitch_5way
P6: COMMS; Connector_3.5mm_Pitch_6way

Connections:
+3V3: P4.7, P5.2; also elsewhere on the board
+12V: P4.1, P5.1; also elsewhere on the board
/BugBridge Micro/EXT_1: P4.3; also elsewhere on the board
/BugBridge Micro/EXT_2: P4.4; also elsewhere on the board
/BugBridge Micro/EXT_3: P4.5; also elsewhere on the board
/BugBridge Micro/EXT_4: P4.6; also elsewhere on the board
/BugBridge Micro/EXT_5: P5.3; also elsewhere on the board
/BugBridge Micro/EXT_6: P5.4; also elsewhere on the board
/BugBridge Micro/RS-485_A: P6.1, P6.4; also elsewhere on the board
/BugBridge Micro/RS-485_B: P6.2, P6.5; also elsewhere on the board
/BugBridge Power/BATT+: P1.1, P3.1; also elsewhere on the board
/BugBridge Power/MOTOR_A: P2.1; also elsewhere on the board
/BugBridge Power/MOTOR_B: P2.2; also elsewhere on the board
GND: P1.2, P3.2, P4.2, P4.8, P5.5, P6.3, P6.6; also elsewhere on the board

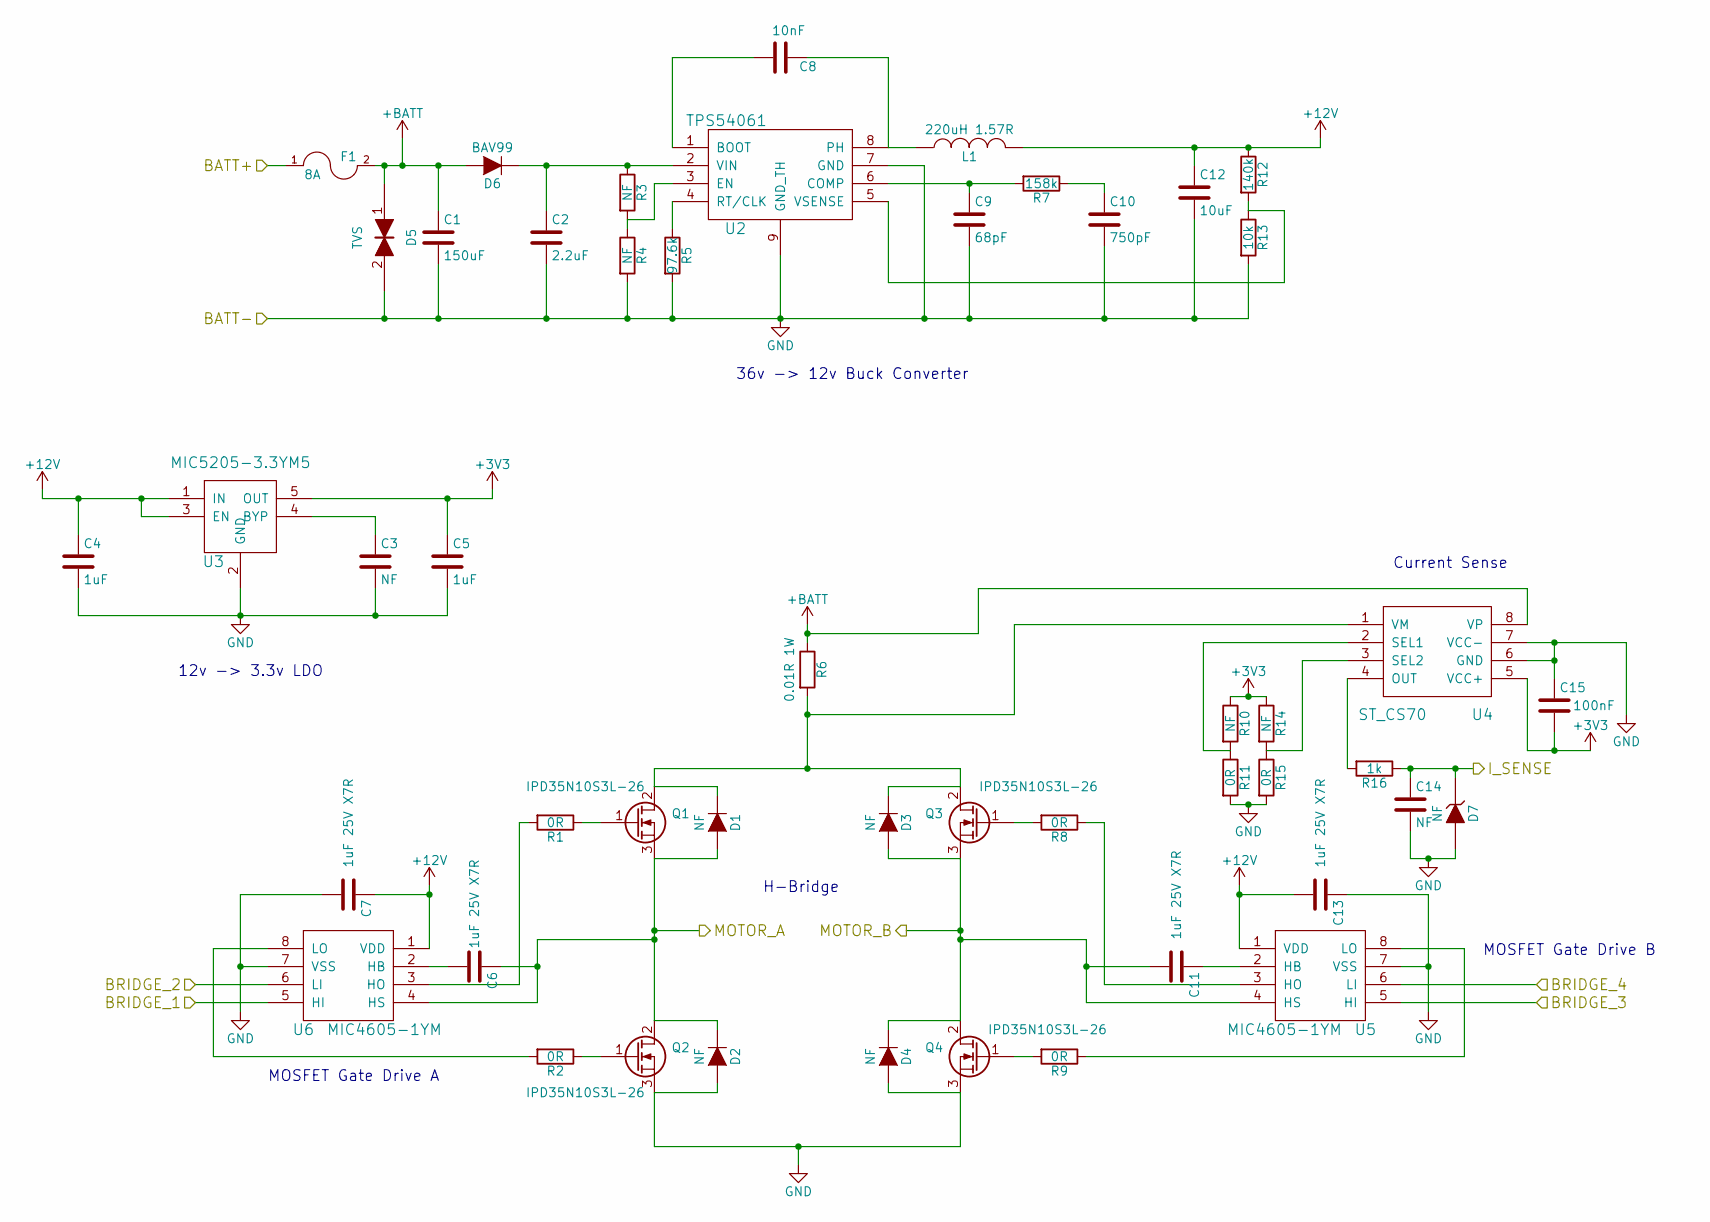
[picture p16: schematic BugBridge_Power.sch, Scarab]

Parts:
C1: 150uF; C_Radial_D10_L20_P5
C2: 2.2uF; C_1206_HandSoldering
C3, C14: NF; C_0805_HandSoldering
C4, C5: 1uF; C_0805_HandSoldering
C6, C7, C11, C13: 1uF 25V X7R; C_0805_HandSoldering
C8: 10nF; C_0805_HandSoldering
C9: 68pF; C_0805_HandSoldering
C10: 750pF; C_0805_HandSoldering
C12: 10uF; C_0805_HandSoldering
C15: 100nF; C_0805_HandSoldering
D1, D2, D3, D4: NF; SMC_Handsoldering
D5: TVS; SMB_Handsoldering
D6: BAV99; SOT-23_Handsoldering
D7: NF; SOT-23
F1: 8A; Fuseholder_5x20_Schurter
L1: 220uH 1.57R; INDUCTOR_SDR0604
Q1, Q2, Q3, Q4: IPD35N10S3L-26; TO-252-2Lead
R1, R2, R8, R9, R11, R15: 0R; R_0805_HandSoldering
R3, R4, R10, R14: NF; R_0805_HandSoldering
R5: 97.6k; R_0805_HandSoldering
R6: 0.01R 1W; R_2512_HandSoldering
R7: 158k; R_0805_HandSoldering
R12: 140k; R_0805_HandSoldering
R13: 10k; R_0805_HandSoldering
R16: 1k; R_0805_HandSoldering
U2: TPS54061; VSON8
U3: MIC5205-3.3YM5; SOT-23-5
U4: ST_CS70; TSSOP8
U5, U6: MIC4605-1YM; SOIC-8_Pitch1.27mm

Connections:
+3V3: C5.1, C15.2, R10.1, R14.1, U3.5 (OUT), U4.5 (VCC+); also elsewhere on the board
+12V: C4.1, C7.1, C12.1, C13.2, L1.2, R12.1, U3.1 (IN), U3.3 (EN), U5.1 (VDD), U6.1 (VDD); also elsewhere on the board
+BATT: C1.1, D5.1, D6.2 (A), F1.2, R6.1, U4.8 (VP); also elsewhere on the board
/BugBridge Micro/BRIDGE_1: U6.5 (HI); also elsewhere on the board
/BugBridge Micro/BRIDGE_2: U6.6 (LI); also elsewhere on the board
/BugBridge Micro/BRIDGE_3: U5.5 (HI); also elsewhere on the board
/BugBridge Micro/BRIDGE_4: U5.6 (LI); also elsewhere on the board
/BugBridge Micro/I_SENSE: C14.1, D7.1 (K), R16.1; also elsewhere on the board
/BugBridge Power/BATT+: F1.1; also elsewhere on the board
/BugBridge Power/MOTOR_A: C6.1, D1.2 (A), D2.1 (K), Q1.3 (S), Q2.2 (D), U6.4 (HS); also elsewhere on the board
/BugBridge Power/MOTOR_B: C11.2, D3.2 (A), D4.1 (K), Q3.3 (S), Q4.2 (D), U5.4 (HS); also elsewhere on the board
GND: C1.2, C2.2, C3.2, C4.2, C5.2, C7.2, C9.2, C10.2, C12.2, C13.1, C14.2, C15.1, D2.2 (A), D4.2 (A), D5.2, D7.2 (A), Q2.3 (S), Q4.3 (S), R4.2, R5.2, R11.2, R13.2, R15.2, U2.7 (GND), U2.9 (GND_TH), U3.2 (GND), U4.6 (GND), U4.7 (VCC-), U5.7 (VSS), U6.7 (VSS); also elsewhere on the board
unnamed: C2.1, D6.1 (K), R3.1, U2.2 (VIN)
unnamed: C3.1, U3.4 (BYP)
unnamed: C6.2, U6.2 (HB)
unnamed: C8.1, L1.1, U2.8 (PH)
unnamed: C8.2, U2.1 (BOOT)
unnamed: C9.1, R7.2, U2.6 (COMP)
unnamed: C10.1, R7.1
unnamed: C11.1, U5.2 (HB)
unnamed: D1.1 (K), D3.1 (K), Q1.2 (D), Q3.2 (D), R6.2, U4.1 (VM)
unnamed: Q1.1 (G), R1.1
unnamed: Q2.1 (G), R2.1
unnamed: Q3.1 (G), R8.2
unnamed: Q4.1 (G), R9.2
unnamed: R1.2, U6.3 (HO)
unnamed: R2.2, U6.8 (LO)
unnamed: R3.2, R4.1, U2.3 (EN)
unnamed: R5.1, U2.4 (RT/CLK)
unnamed: R8.1, U5.3 (HO)
unnamed: R9.1, U5.8 (LO)
unnamed: R10.2, R11.1, U4.2 (SEL1)
unnamed: R12.2, R13.1, U2.5 (VSENSE)
unnamed: R14.2, R15.1, U4.3 (SEL2)
unnamed: R16.2, U4.4 (OUT)

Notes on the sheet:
36v -> 12v Buck Converter
12v -> 3.3v LDO
Current Sense
H-Bridge
MOSFET Gate Drive A
MOSFET Gate Drive B

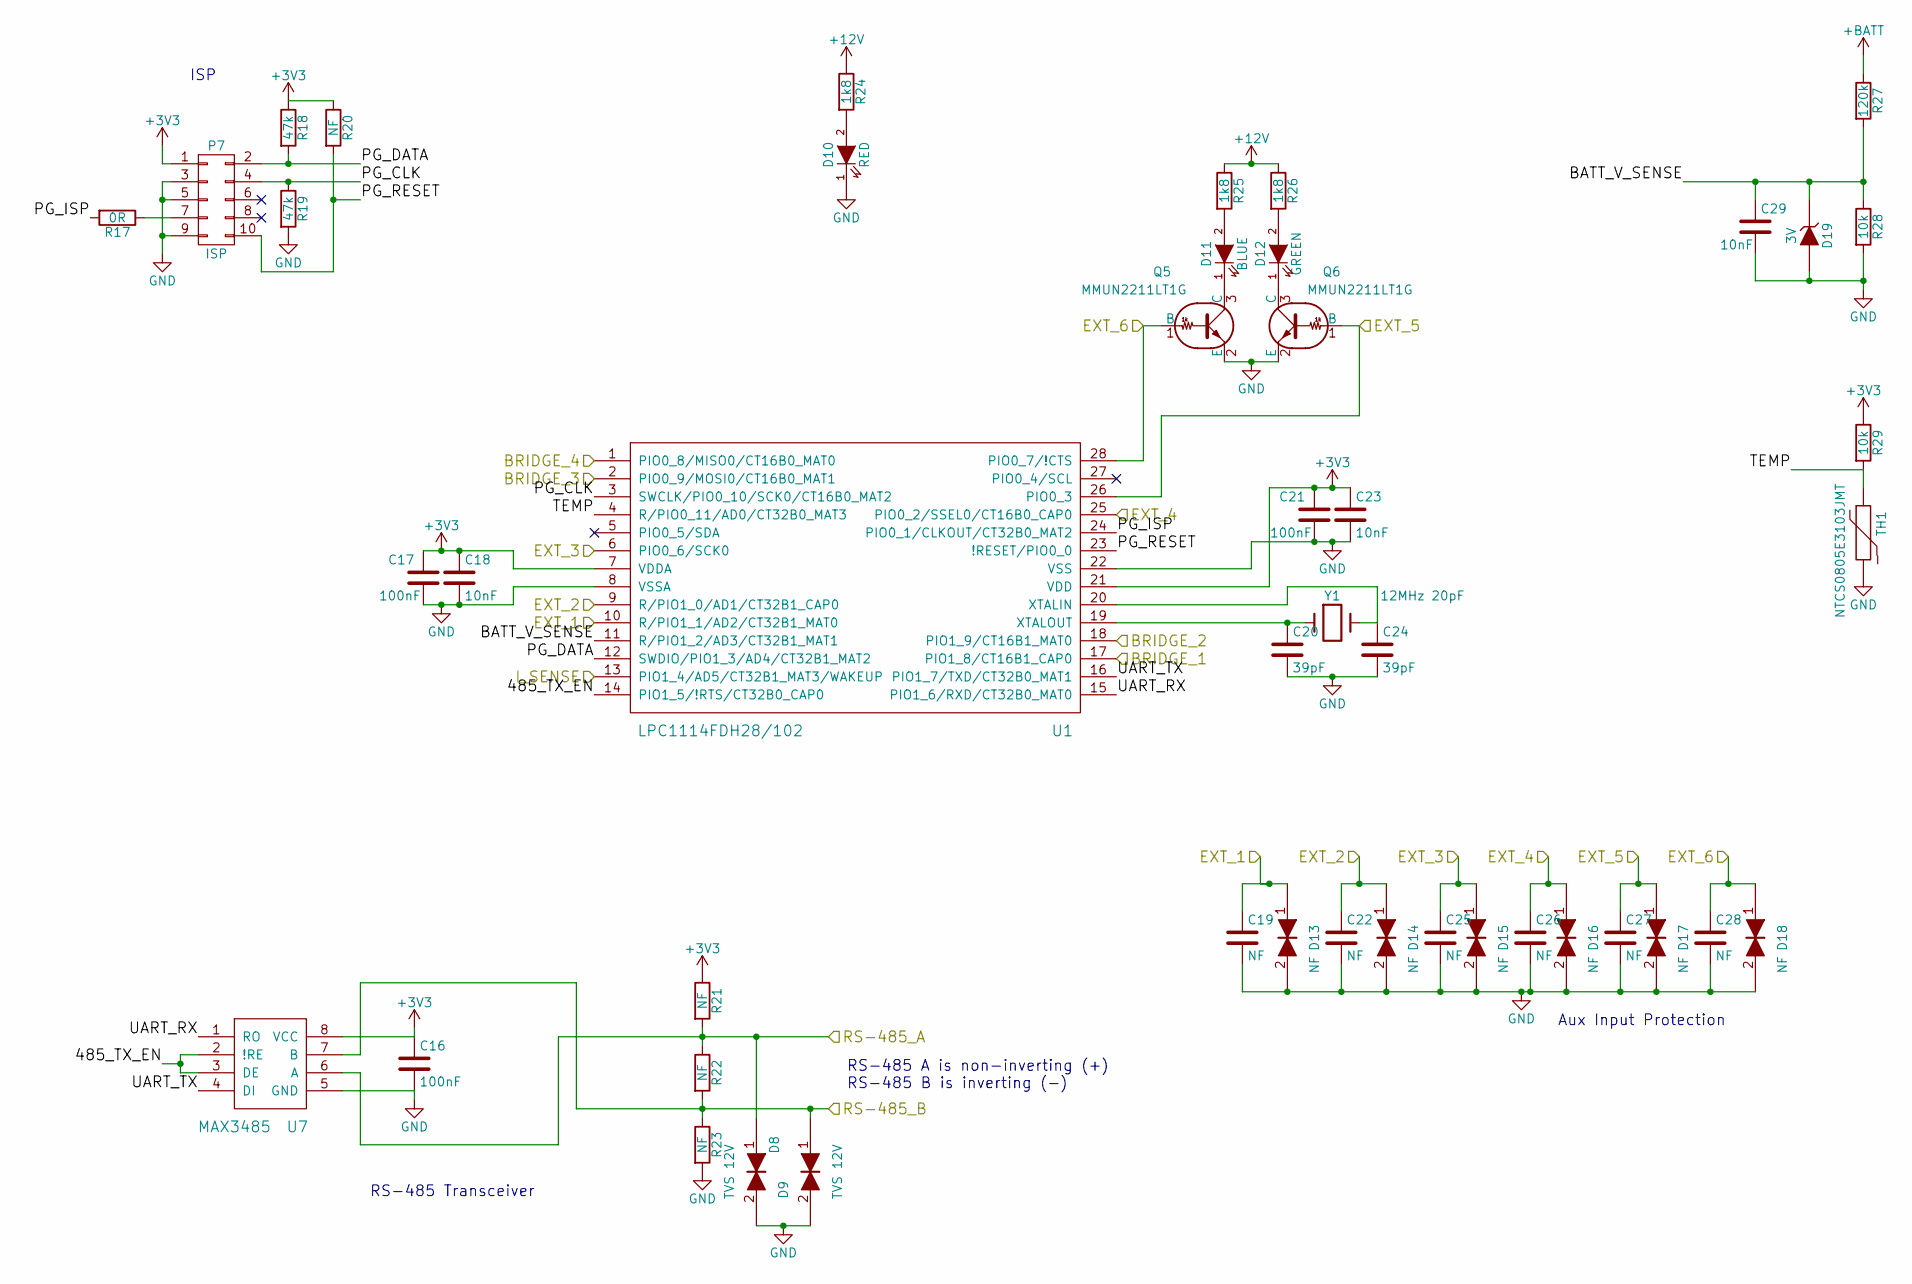
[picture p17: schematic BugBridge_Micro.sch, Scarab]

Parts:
C16, C17, C21: 100nF; C_0805_HandSoldering
C18, C23, C29: 10nF; C_0805_HandSoldering
C19, C22, C25, C26, C27, C28: NF; C_0805_HandSoldering
C20, C24: 39pF; C_0805_HandSoldering
D8, D9: TVS 12V; DO-214AC_Handsoldering
D10: RED; LED_0805
D11: BLUE; LED_0805
D12: GREEN; LED_0805
D13, D14, D15, D16, D17, D18: NF; DO-214AC_Handsoldering
D19: 3V; SOT-23
P7: ISP; CON_02X05_1.27
Q5, Q6: MMUN2211LT1G; SOT-23_Handsoldering
R17: 0R; R_0805_HandSoldering
R18, R19: 47k; R_0805_HandSoldering
R20, R21, R22, R23: NF; R_0805_HandSoldering
R24, R25, R26: 1k8; R_0805_HandSoldering
R27: 120k; R_0805_HandSoldering
R28, R29: 10k; R_0805_HandSoldering
TH1: NTCS0805E3103JMT; R_0805_HandSoldering
U1: LPC1114FDH28/102; TSSOP-28
U7: MAX3485; SOIC-8_Pitch1.27mm
Y1: 12MHz 20pF; Crystal_FOX_HC

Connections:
+3V3: C16.1, C17.1, C18.1, C21.1, C23.1, P7.1, R18.1, R20.1, R21.1, R29.1, U1.7 (VDDA), U1.21 (VDD), U7.8 (VCC); also elsewhere on the board
+12V: R24.1, R25.1, R26.1; also elsewhere on the board
+BATT: R27.1; also elsewhere on the board
/BugBridge Micro/485_TX_EN: U1.14 (PIO1_5/!RTS/CT32B0_CAP0), U7.2 (!RE), U7.3 (DE)
/BugBridge Micro/BATT_V_SENSE: C29.1, D19.1 (K), R27.2, R28.1, U1.11 (R/PIO1_2/AD3/CT32B1_MAT1)
/BugBridge Micro/BRIDGE_1: U1.17 (PIO1_8/CT16B1_CAP0); also elsewhere on the board
/BugBridge Micro/BRIDGE_2: U1.18 (PIO1_9/CT16B1_MAT0); also elsewhere on the board
/BugBridge Micro/BRIDGE_3: U1.2 (PIO0_9/MOSI0/CT16B0_MAT1); also elsewhere on the board
/BugBridge Micro/BRIDGE_4: U1.1 (PIO0_8/MISO0/CT16B0_MAT0); also elsewhere on the board
/BugBridge Micro/EXT_1: C19.1, D13.1, U1.10 (R/PIO1_1/AD2/CT32B1_MAT0); also elsewhere on the board
/BugBridge Micro/EXT_2: C22.1, D14.1, U1.9 (R/PIO1_0/AD1/CT32B1_CAP0); also elsewhere on the board
/BugBridge Micro/EXT_3: C25.1, D15.1, U1.6 (PIO0_6/SCK0); also elsewhere on the board
/BugBridge Micro/EXT_4: C26.1, D16.1, U1.25 (PIO0_2/SSEL0/CT16B0_CAP0); also elsewhere on the board
/BugBridge Micro/EXT_5: C27.1, D17.1, Q6.1 (B), U1.26 (PIO0_3); also elsewhere on the board
/BugBridge Micro/EXT_6: C28.1, D18.1, Q5.1 (B), U1.28 (PIO0_7/!CTS); also elsewhere on the board
/BugBridge Micro/I_SENSE: U1.13 (PIO1_4/AD5/CT32B1_MAT3/WAKEUP); also elsewhere on the board
/BugBridge Micro/PG_CLK: P7.4, R19.1, U1.3 (SWCLK/PIO0_10/SCK0/CT16B0_MAT2)
/BugBridge Micro/PG_DATA: P7.2, R18.2, U1.12 (SWDIO/PIO1_3/AD4/CT32B1_MAT2)
/BugBridge Micro/PG_ISP: R17.2, U1.24 (PIO0_1/CLKOUT/CT32B0_MAT2)
/BugBridge Micro/PG_RESET: P7.10, R20.2, U1.23 (!RESET/PIO0_0)
/BugBridge Micro/RS-485_A: D8.1, R21.2, R22.1, U7.6 (A); also elsewhere on the board
/BugBridge Micro/RS-485_B: D9.1, R22.2, R23.1, U7.7 (B); also elsewhere on the board
/BugBridge Micro/TEMP: R29.2, TH1.1, U1.4 (R/PIO0_11/AD0/CT32B0_MAT3)
/BugBridge Micro/UART_RX: U1.15 (PIO1_6/RXD/CT32B0_MAT0), U7.1 (RO)
/BugBridge Micro/UART_TX: U1.16 (PIO1_7/TXD/CT32B0_MAT1), U7.4 (DI)
GND: C16.2, C17.2, C18.2, C19.2, C20.2, C21.2, C22.2, C23.2, C24.2, C25.2, C26.2, C27.2, C28.2, C29.2, D8.2, D9.2, D10.1 (K), D13.2, D14.2, D15.2, D16.2, D17.2, D18.2, D19.2 (A), P7.3, P7.5, P7.9, Q5.2 (E), Q6.2 (E), R19.2, R23.2, R28.2, TH1.2, U1.8 (VSSA), U1.22 (VSS), U7.5 (GND); also elsewhere on the board
unnamed: C20.1, U1.19 (XTALOUT), Y1.1
unnamed: C24.1, U1.20 (XTALIN), Y1.2
unnamed: D10.2 (A), R24.2
unnamed: D11.1 (K), Q5.3 (C)
unnamed: D11.2 (A), R25.2
unnamed: D12.1 (K), Q6.3 (C)
unnamed: D12.2 (A), R26.2
unnamed: P7.7, R17.1

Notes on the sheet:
RS-485 A is non-inverting (+) RS-485 B is inverting (-)
Aux Input Protection
ISP
RS-485 Transceiver

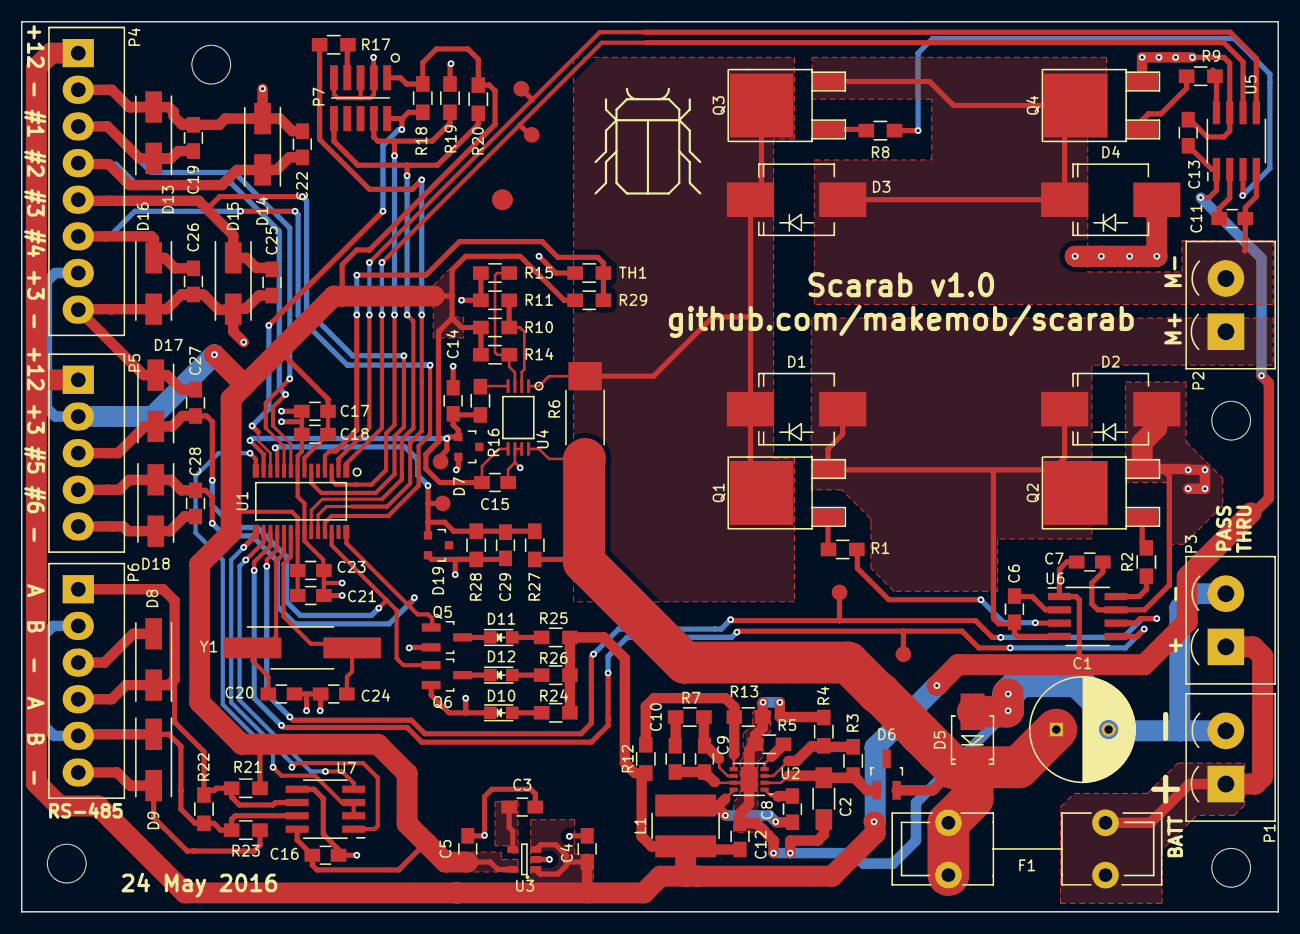
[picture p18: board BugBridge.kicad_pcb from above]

Board: 2 copper layers, 120.0 x 85.0 mm, 101 parts (0 on the bottom side), 60 nets.

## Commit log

2016-07-14 v1.0 BOM for quote
    [Scarab v1.0 BOM For Quote 20160714.csv, Scarab v1.0 BOM For Quote 20160714.xlsx]
2016-07-26 BOM with pricing
    [Scarab v1.0 BOM With Pricing 20160714.xlsx]
2016-08-08 BOM for quote 20160806
    [Scarab v1.0 BOM For Quote 20160806.xlsx]
2016-08-16 BOM for quote 20160817
    [Scarab v1.0 BOM For Quote 20160817.xlsx]
2018-12-29 Update encoder wiring diagram
